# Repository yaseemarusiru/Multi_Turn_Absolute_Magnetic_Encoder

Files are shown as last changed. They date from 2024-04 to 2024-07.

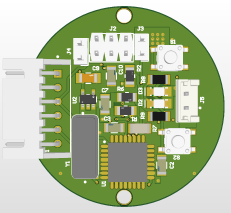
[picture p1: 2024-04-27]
PCB/Encoder PCB/Project Outputs for EDR/PCB_Photos/bottom.png

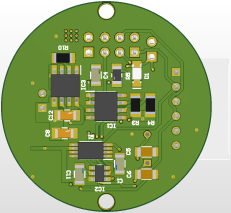
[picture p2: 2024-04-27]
PCB/Encoder PCB/Project Outputs for EDR/PCB_Photos/top.png

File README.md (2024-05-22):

# Multi_Turn_Absolute_Magnetic_Encoder
This repository contains all the documents of the project in which we made a multi turn absolute magnetic encoder.

Project team members :
  - <a href="https://github.com/YasodaLAE" target="_blank">Yasoda Lasiru</a>
  - Yaseema Rusiru (myself)
    




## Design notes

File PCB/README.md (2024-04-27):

This folder contains the design files of the PCB we designed using ALtium for this project.

There are 6 schematics in our project. 
  - Microcontroller.SchDoc
  - Voltage Regulator.SchDoc
  - Encode Schematic.SchDoc
  - Hall Effect IC.SchDoc
  - Battery Charger.SchDoc
  - Battery Protection.SchDoc

PCB file is renamed as PCB1.PcbDoc

You can check photos of the PCB in the Project Outputs for EDR folder.

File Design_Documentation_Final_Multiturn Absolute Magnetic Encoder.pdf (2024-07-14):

### Department of Electronic and Telecommunication Engineering University of Moratuwa

### Design Documentation

# Multi-turn Absolute Magnetic Encoder

Epa Y.L.A. | 210156U
Epa Y.R.A. | 210157A

This report is submitted as a partial fulfilment of module EN2160

June 2024

Design Documentation

## Contents

Comprehensive Design Details | 3
1 Introduction | 3
2 Electronics Documentation | 4
3 Enclosure Design | 24
4 Software Documentation | 45
Appendix | 50
A Daily Log | 50

# Comprehensive Design Details

## 1 Introduction

Encoders are devices that convert one form of information into another. They work by detecting the rotation or linear motion of a shaft or axle and converting it into a signal that can be interpreted by a control system. This signal can be used to monitor the position, speed, and direction of the shaft or axle, and to control its motion with high precision.

There are several types of encoders, including incremental encoders, absolute encoders, rotary encoders, and linear encoders.

Incremental encoders provide information about the motion of the shaft, including its direction and the distance it has moved, while absolute encoders provide the exact position of the shaft at any given time. Rotary encoders are used for rotary motion and can be either incremental or absolute, while linear encoders are used for linear motion.

Encoders have a wide range of applications in various industries including manufacturing, automation, aerospace, healthcare and entertainment. They are used in robotics, CNC machines, motors, tachometers, user interfaces and many other systems that require precise control and monitoring of motion and position. Encoders help improve the efficiency, accuracy and safety of machines and systems and they play a crucial role in enabling automation and advanced manufacturing technologies.

### 1.1 Types of Encoders

- Rotary Encoders

– Incremental Rotary Encoders: Measure the change in position from a reference point. They produce two square waves that help determine the direction and distance of rotation. These have a disc with alternating opaque and transparent sectors. As the disc rotates, an LED shines through the sectors, and a photo detector on the other side generates pulses. The number of pulses counted per unit time determines the speed, and the direction can be determined by the phase difference between two output signals.

– Absolute Rotary Encoders: Provides a unique code for each position. These can determine the exact position without requiring a reference point. Also, these have a disc with multiple tracks each with a unique pattern. Each track corresponds to a binary bit of the position code. The combination of all tracks gives a unique binary code for each position.

- Linear Encoders

– Incremental Linear Encoders: Similar to incremental rotary encoders but measures linear displacement. These encoders use a scale with equally spaced marks and a read head that moves along the scale. As the read head moves, it detects the marks and generates pulses.

– Absolute Linear Encoders: Provide an absolute position along a linear path. These encoders use a scale with a unique pattern along its length and a read head that reads the pattern. The pattern provides a unique position code.

- Optical Encoders: These use light (typically LEDs and photodetectors) to detect position changes. Commonly used in high-precision applications.
- Magnetic Encoders: Use magnetic fields to detect position changes. They are robust in harsh environments and less sensitive to dust and other contaminants.

From these types, we are designing a multi turn absolute magnetic encoder.

### 1.2 Uses of Encoders

Encoders are used in various fields for different applications. Below are some common ones.

- Industrial Automation

– Position and speed control in machinery.

– Feedback for robotic arms and CNC machines.

- Consumer Electronics

– Volume controls in audio equipment.

– User interface controls in various devices.

- Automotive Applications

– Steering angle sensors.

– Engine position sensors.

- Aerospace

– Position feedback in control systems.

– Monitoring the position of control surfaces.

- Medical Equipment

– Position sensing in imaging equipment.

– Feedback in robotic surgery tools.

This section includes a detailed description of the electronic components and circuitry of multi-turn absolute magnetic encoder.

## 2 Electronics Documentation

### 2.1 Components Selection

Our main components include selecting a hall effect sensor IC, a magnet for the placement on the shaft, a microcontroller and power management circuit components which includes a battery and power regulation and management ICs.

### 2.1.1 Sensing Circuit

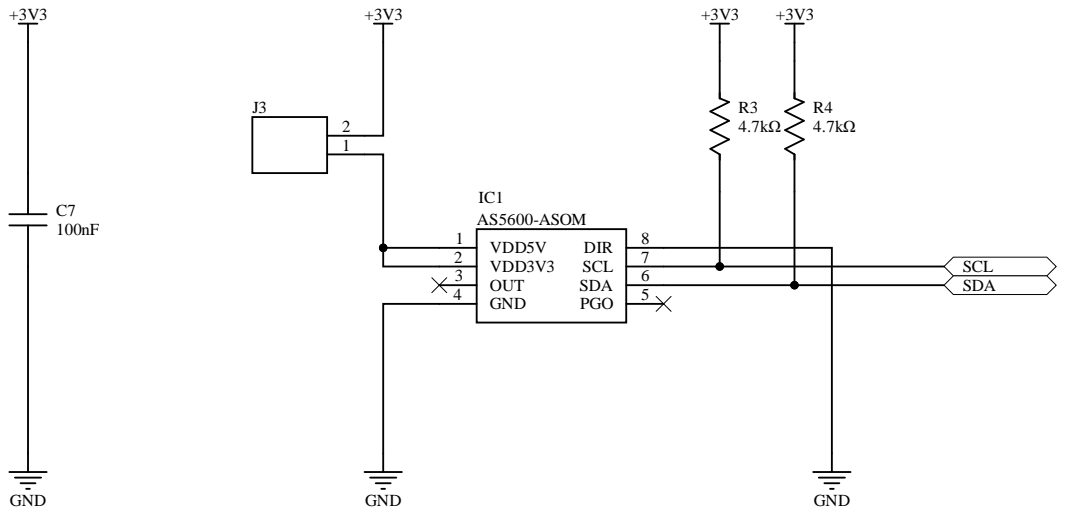
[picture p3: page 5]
Title; Size; Number; Revision; Date:; Sheet of; File:; F:\Altium Projects\..\Hall Effect IC.SchDoDc rawn By:; VDD5V 1 VDD3V3 2 OUT 3 GND 4; DIR; SCL; SDA; PGO; IC1 AS5600-ASOM; GND; SCL SDA; Yasoda Lasiru

Hall Effect IC

Through the sensing circuit, we detect the magnetic field change of a diametrically magnetized magnet using hall effect sensor IC which is placed on axis to the magnet. Important information such as the specifications of the magnet to select, according to the hall effect sensor IC, the air gap between the IC and the magnet etc. are presented below. They were obtained after a thorough analysis of the datasheet of the select hall effect sensor IC - AS5600 - which is manufactured by a leading company in the field -AMS OSRAM.

AS5600 hall effect sensor IC works in 3.3V. For that we have to connect VDD5V and VDD3V3 together and connect to 3.3V. A separate power isolation jumper J3 is used here so that we can disconnect the hall effect IC from the ATMega328p while we are programming the microcontroller. To pull up the I2C lines SCL and SDA, we have used R3 and R4 which are 4.7kΩ . This value is selected as per the datasheet of AS5600. Since we are reading the angle value through I2C we do not need to use OUT pin - which outputs the angle value in a PWM signal. PGO pin is used to enter the programming mode of the AS5600. Since we are using the default configurations, we won’t be needing that pin as well. The C7 100nF capcitor is use between the power lines according to the recommendation of the datasheet.

AS5600 Hall Effect Sensor

AS5600 is a Hall-effect based rotary magnetic position sensor. It uses planar sensors that convert the magnetic field component perpendicular to the surface of the chip into a voltage. The signals coming from the Hall sensors are first amplified and filtered before being converted by the analog-to-digital converter (ADC) inside the IC.

This sensor IC measures the absolute angle of a diametric magnetized on-axis magnet. The chip contains 4 hall effect sensors arranged in a circle. Together, they can detect changes in the direction of the magnetic field.

- Resolution of 12 bits
- temperature range of -40°C to 125°C
- supply voltage range -0.3V to 6.1V
- power continuous consumption of 50mW at 70°C
- Analog and PWM outputs
- PWM output frequency upto 920Hz
- I2C interfacing option
- programmable start and zero angle
- automatic entry into low power mode operation

There are various hall effect sensor ICs in the global market to choose from. Below are the criteria which led to the selection of the AS5600 magnetic hall effect sensor IC.

- Output Resolution: The AS5600 has a 12-bit digital to analog conversion (DAC) output resolution
- Maximum Angle Programmable: You can program the maximum angle from 18 to 360 degrees

- Selectable Output: The AS5600 provides an analog output ratiometric to VDD or PWM-encoded digital output
- Low-Power Consumption: The AS5600 has a smart low power mode feature to automatically reduce the power consumption
- Easy Setup: The AS5600 has automatic magnet detection
- Robust Environmental Tolerance: The AS5600 is qualified for a temperature range from -40°C to 125°C
- Magnet Airgap: The typical airgap is between 0.5 mm and 3 mm, and it depends on the selected magnet. A larger and stronger magnet allows a larger airgap

Magnet

According to the AS5600 data-sheet, the recommended specifications of the magnet are as follows.

- Diametrically magnetized: cylindrical
- Any one of diameter 6mm and thickness of 2.5mm, diameter 8mm and thickness of 3mm or diameter 8mm and thickness of 4mm
- magnetic input range should be between 30-90mT

We have selected a cylindrical neodymium magnet of diameter 6mm and thickness of 2.5mm.

### 2.2.1 Microcontroller Circuit

We have used a switch S1 to reset the microcontroller. It’s pulled up through R1 10kΩ resistor and connected to ground through C3 100nF capacitor.

Also, we have used another switch in the circuit, which is used to manually tare the turned angle, used for debugging purposes. Same as S1, it’s pulled up through R2 10kΩ and connected to ground through C4 100nF capacitor.

J2 is the programming port which is used to program the microcontroller. These SPI pins are also connected separately to the communication port, which is available to the user. Since we aim to minimize power consumption, we are using Y1 8MHz crystal oscillator as per the recommendation of the datasheet. This is connected to ground through two 22pF capacitors - which are also chosen according to the datsheet.

We have also used 100nF capacitors here to suppress high frequency noise and stabilize the voltage.

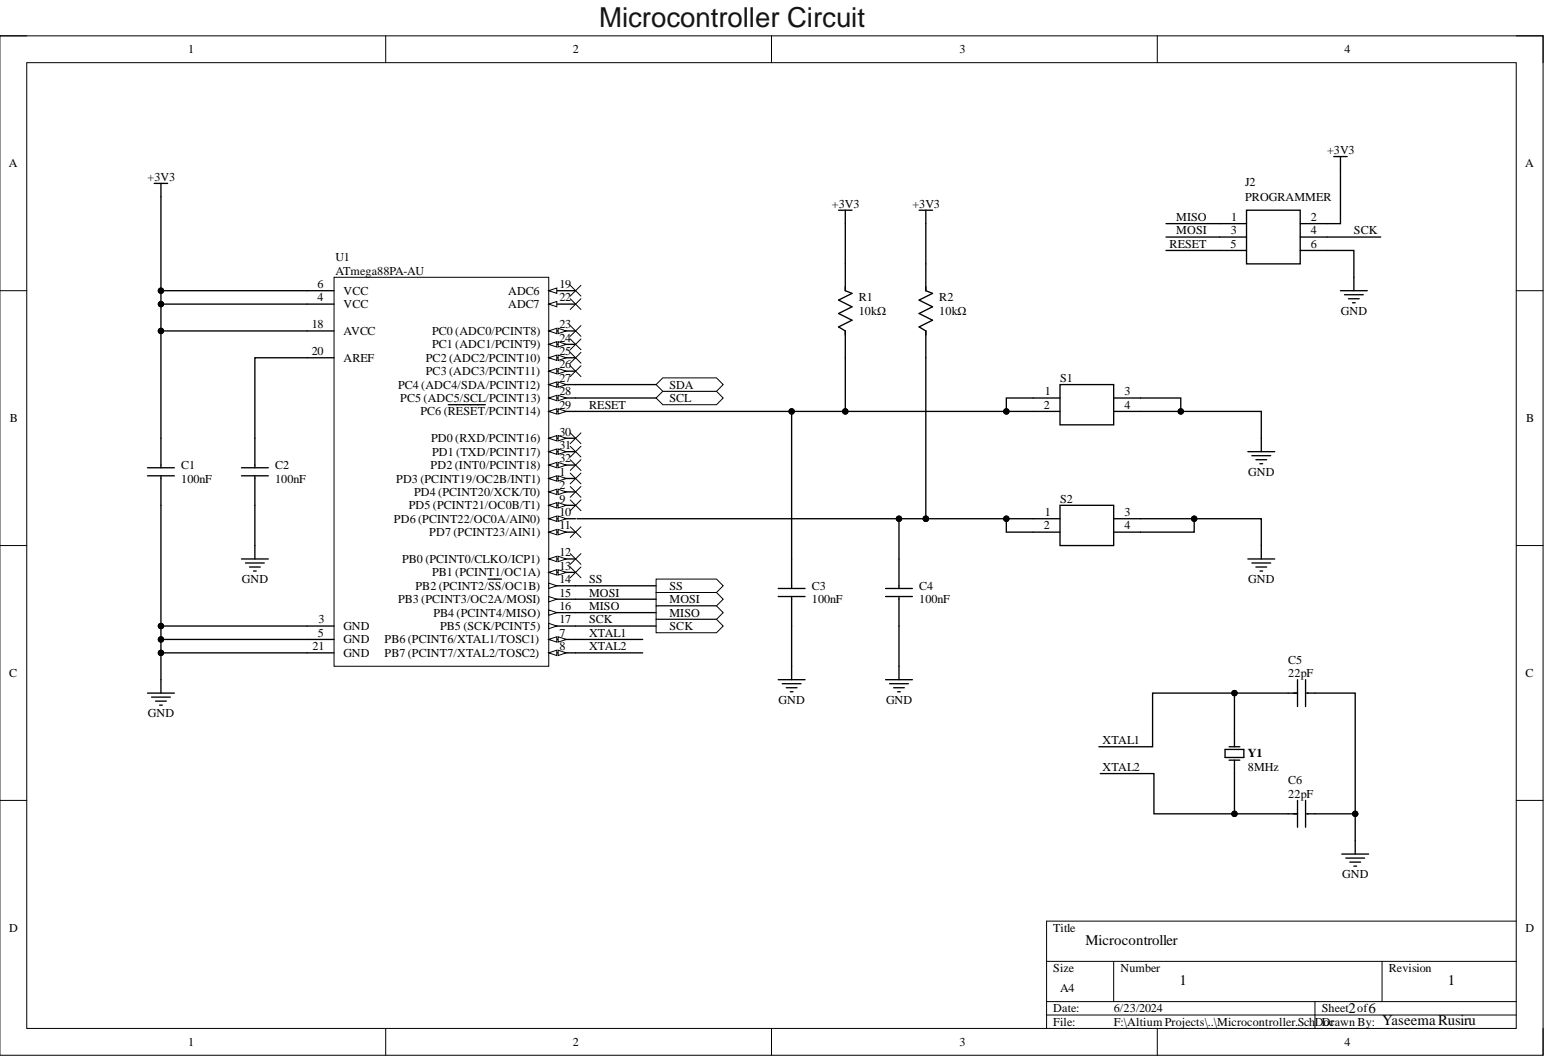
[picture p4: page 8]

ATMega328P-AU

We are using ATMega328P-AU as the micro-controller for our multi turn absolute magnetic encoder. It is a low power consuming microcontroller which can implement both SPI and I2C communication protocols at the same time, while saving power. It interfaces with the AS5600 sensor module to process position data and generate output signals. This includes the absolute angle and the algorithm to count the number of turns.

- 8 bit AVR RISC based
- 8KB flash memory 512B EEPROM and 1KB SRAM
- 10 bit ADC
- 8 bit timer/counter with prescalar and two PWM channels
- Internal calibrated oscillator

We have considered the following criteria when selecting thee microcontroller.

- CPU Architecture: The ATMega328P-AU is based on the AVR RISC architecture1. This architecture is known for its high performance and power efficiency
- Memory: The ATMega328P-AU has 32KB of in-system programmable flash memory, 1KB of EEPROM, and 2KB of internal SRAM. These are required for our application
- Operating Voltage: The ATMega328P-AU operates between 1.8-5.5V. We opted for 3.3V in order to run at a speed of 8MHz.
- Power Efficiency
- Seperate I2C and SPI bus availability to read AS5600 IC data while also giving the angle output to the user through SPI interface
- Availability

### 2.3.1 Power Management

As the main power supply for the hall effect sensor IC and the microcotroller, the user should input an external power source within the given voltage range (3.4V to 8V). Through this supply, the rechargeable battery charges, allowing the system to utilize its’ power even during power outages. For this we have implemented a separate charging circuit with over current and voltage protection.

Since we intend to use the microcontroller and the hall effect sensor IC with 3.3V supply, a voltage regulator is also to be used as part of the power management circuit. Moreover, we have utilized low power modes in both the microcontroller and the hall effect sensor IC in order to ensure that the power used is minimized. Furthermore this sub assembly consists of TP4056 and FS8205A ICs.

Voltage Regulator Circuit

J4 power isolation connector is used to isolate the microcontroller from the LDO while programming. So, we should power the microcontroller through the programming port while programming.

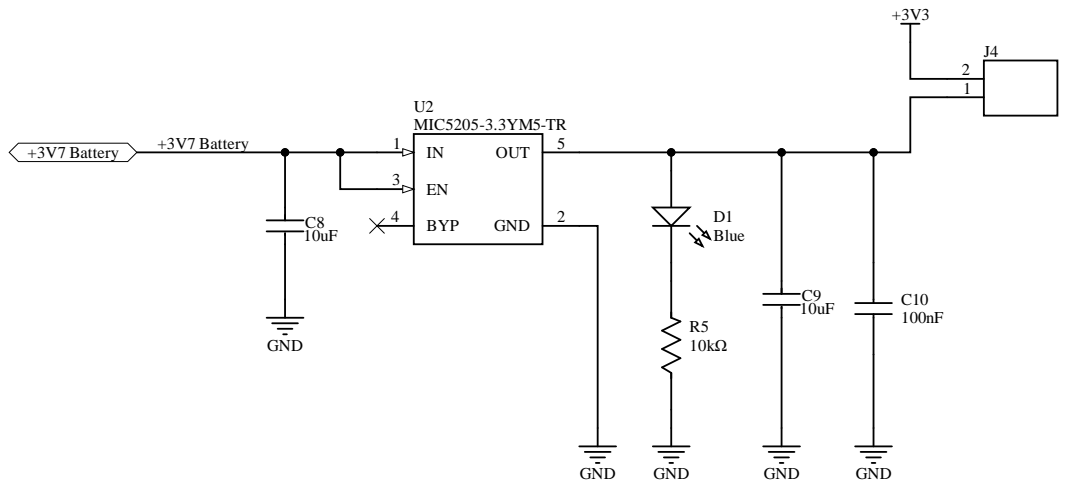
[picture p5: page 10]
Title; Size; Number; Revision; Date:; Sheet of; File:; F:\Altium Projects\..\Voltage Regulator.SchDDrawoc n By:; VoltageRegulator; BYP 4; OUT; GND; U2 MIC5205-3.3YM5-TR; +3V7 Battery +3V7 Battery; Blue; Yasoda Lasiru

We have used D1 blue diode to indicate whether power is available - specifically 3.3V which is available at the OUT pin. Here we have used 10kΩ resistor to minimize the current used by the diode. The datasheet of MIC5205-3.3YM5-TR LDO specifically mentions to use a capacitor value greater than 2.2 uF between ground and the OUT pin.

Since enable/shutdown is not required in our application, we have connected IN and EN pins (according to the datasheet).

Since noise is not a major concern BYP pin is not connected according to the datasheet. To handle the input voltage fluctuations, C8 10uF capacitor is used.

MIC5205-3.3YM5-TR Low-dropout Voltage Regulator

The MIC5205-3.3YM5-TR is a low-dropout (LDO) voltage regulator. It is designed to deliver a fixed output of 3.3V. This LDO regulator is commonly used in battery-powered devices due to its low quiescent current of 10nA and it provides good line and load regulation characteristics.

- Operating temperature range -40 - 125°C
- 150mA typical output current
- Output Voltage Accuracy: The MIC5205-3.3YM5-TR offers better than 1% initial accuracy
- Low Dropout Voltage: The MIC5205-3.3YM5-TR as a very low dropout voltage (typically 17 mV at light loads and 165 mV at 150 mA)12. This low dropout voltage allows the regulator to operate efficiently even when the input voltage is only slightly above the output voltag
- Temperature Coefficient: The MIC5205-3.3YM5-TR has a very low temperature coefficient
- Load and Line Regulation: The MIC5205-3.3YM5-TR provides extremely tight load and line regulation

Battery Charger Circuit

A high input in the CE pin will put the TP4056 in the normal operating mode. Hence, we have attached VCC to CE pin. The positive terminal of the battery should be connected to the BAT pin.

PROG pin is used to set the constant charge current and it can be used to monitor the charge current. This pin is grounded through a 2kΩ resistor. It sets the charging current which is 580mA according to the datasheet. BAT pin provides charge current to the battery and provides regulation voltage of 4.2V. When the voltage of the VIN pin drops to within 30mV of the BAT pin voltage, TP4056 enters low power sleep mode. This drops the BAT pin’s current to less than 2uA.

We can get an idea about the charging state of the battery through the intensity of the D2 and D3 LEDs.

Charge state | Orange LED | Green LED
charging | ON | OFF
Charge Termination | OFF | ON
Vin too low/ no battery | OFF | OFF

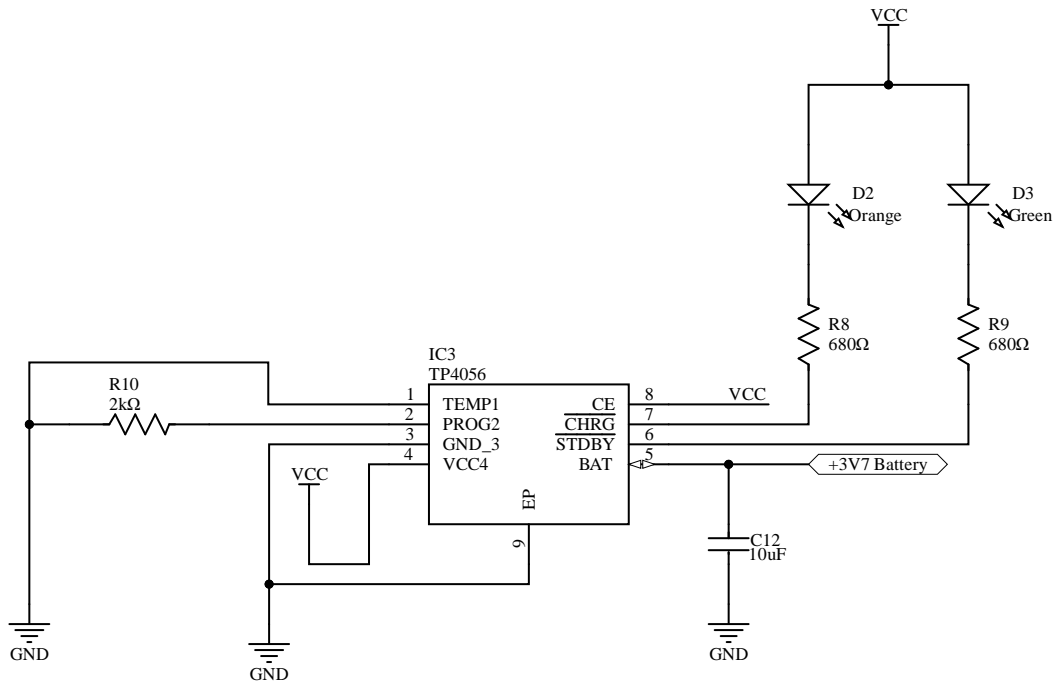
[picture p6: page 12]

TP4056 Constant Current Constant Voltage Linear Charger IC

The TP4056 is a standalone linear charger IC designed for single cell lithium-ion batteries. The charge current can be programmed externally with a single resistor. We have used 2kΩ for this. As per the datasheet, the charging current then becomes 580mA.

- Programmable charge current upto 1A
- Linear charger for single cell Lithiom Ion batteries
- Constant current
- Constant voltage
- Input supplt voltage -0.3V - 8V
- Maximum junction temperature 145
- Operating temperature range -40 - 85°C

Battery Protection Circuit

External battery can be connected to the circuit through J5. Positive and negative terminals of the battery are connected to VCC and GND pins through R6. C1 and R6 are selected according to the specifications given in the datasheet. R7 resistor value is also given in the datasheet. Since TD pin is used for testing purposes, it is not used. CS input pin is used for current sensing and detecting the charging.

Both S1 1 pin and S1 2 pin are the same. Both S2 1 pin and S2 2 pin are the same. G1 is the gate of one N channel MOSFET. G2 is the gate of the other N channel MOSFET. S1 1 is the source of the first MOSFET, S2 1 is the source of the second MOSFET. Hence these pins are grounded here. OD pin of DW01A-G is used to connect MOSFET gate for discharge control. OC pin is also connected to a MOSFET gate for charge control.

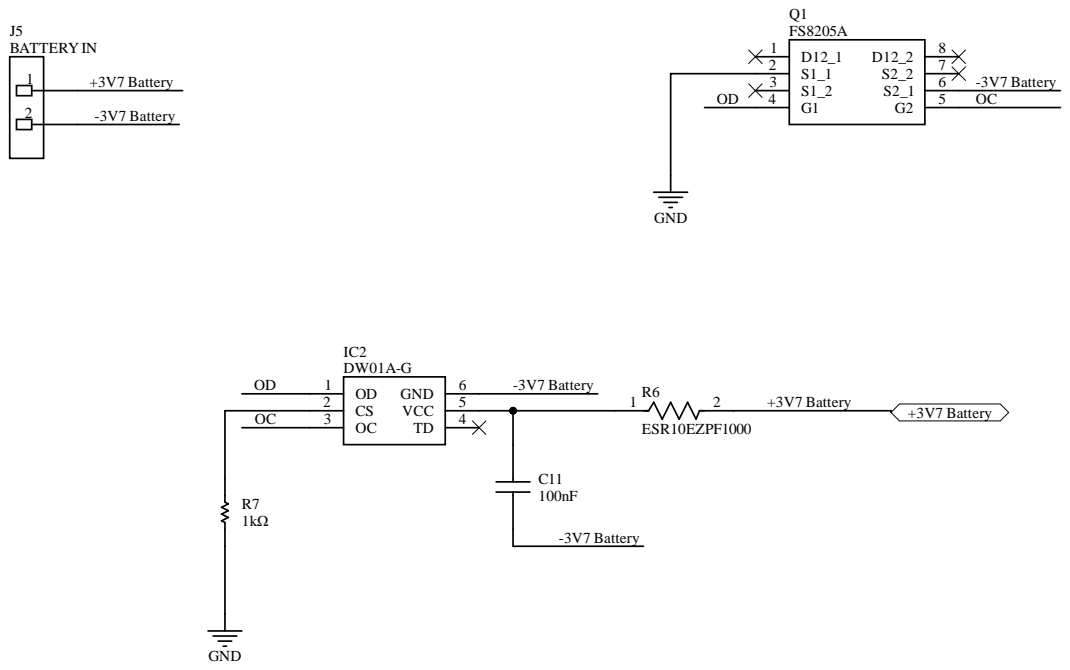
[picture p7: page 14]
Title; Size; Number; Revision; Date:; Sheet of; File:; F:\Altium Projects\..\Battery Protection.ScDhDrawoc n By:; J5 BATTERY IN; -3V7 Battery; GND; VCC; +3V7 Battery; Battery ProtectionCircuit; ESR10EZPF1000; YaseemaRusiru

FS8205A Dual N Channel Power MOSFET

This IC is used to ensure safe and efficient charging and discharging of the battery, preventing overcharging or excessive discharge which could damage the battery.

- Drain source voltage 20V
- Continuous drain current at 25°C - 6A
- Total power dissipation at 25°C - 1W
- Operating junction temperature range -55 to 150°C

DW01A-G Battery Protection IC

The DW01A-G is a one cell Lithium-ion/Polymer battery protection IC. It is designed to protect lithium-ion/polymer batteries from damage or degrading the lifetime due to overcharge, overdischarge, and/or overcurrent for one-cell lithium-ion/polymer battery powered systems. The DW01A-G ensures that the battery operates within its safe limits, thereby extending its lifespan and maintaining its performance

- Overcharge detection voltage 4.30±0.05V
- Overcharge release voltage 4.10±0.05V
- Overdischarge detection voltage 2.40±0.10V
- Overdischarge release voltage 3.00±0.10V
- Supply current at 3.9V VCC typical 3µA max 6µA

### 2.7 Functional Block Diagram

Figure 1: Functional Block Diagram of the Selected Design

### 2.8 System Overview

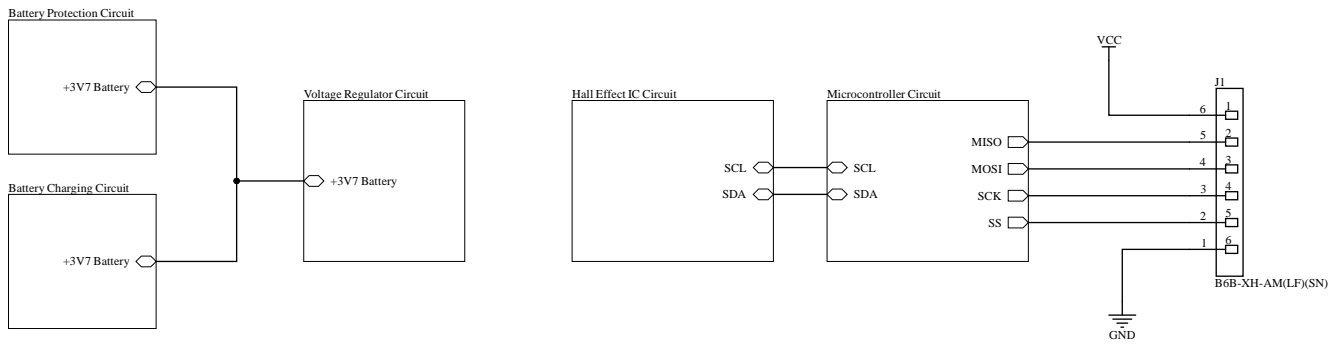
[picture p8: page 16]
Title; Size; Number; Revision; Date:; Sheet of; File:; F:\Altium Projects\..\Encode Schematic.SchDDrawocn By:; MOSI; MISO; SCK; SCL; SDA; Microcontroller Circuit; +3V7 Battery; GND; VCC; Encoder Circuit; YaseemaRusiru; PIJ101; PIJ102; PIJ103; PIJ104; PIJ105; PIJ106; COJ1

Battery Protection Circuit

Voltage Regulator Circuit

Hall Effect IC Circuit

Battery Charging Circuit

### 2.10 PCB Design

### 2.10.1 PCB Specifications

- Material: FR4
- Thickness: 1.6mm
- Copper Weight: 1 oz
- Radius : 18mm

2.10.2 2D Layout

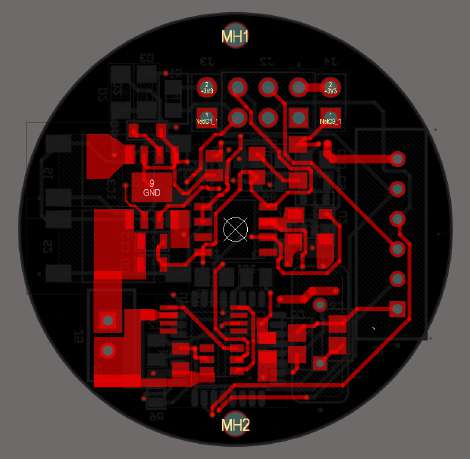
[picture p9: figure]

Figure 2: Top Layer

Figure 3: Bottom Layer

### 2.10.3 Before Soldering PCB

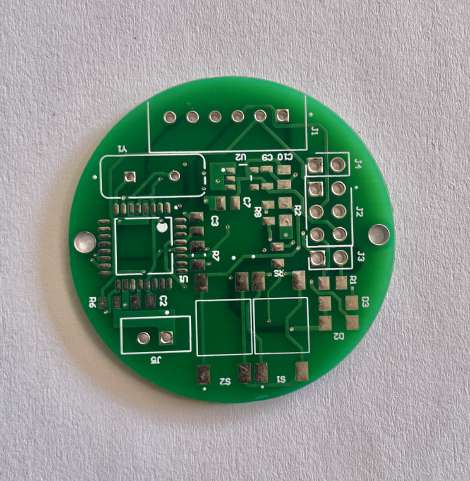
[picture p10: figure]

Figure 4: Bare PCB - Top

Figure 5: Bare PCB - Bottom

### 2.10.4 After Soldering PCB

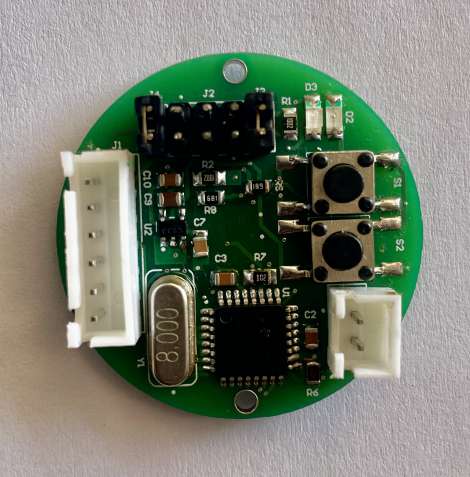
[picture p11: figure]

Figure 6: Soldered PCB

Figure 7: Soldered PCB

### 2.10.5 Photographs as evidence for the PCB testing

Here motor is controlled through raspberry pi and the encoder data is collected from the raspberry pi to be shown on the dashboard.

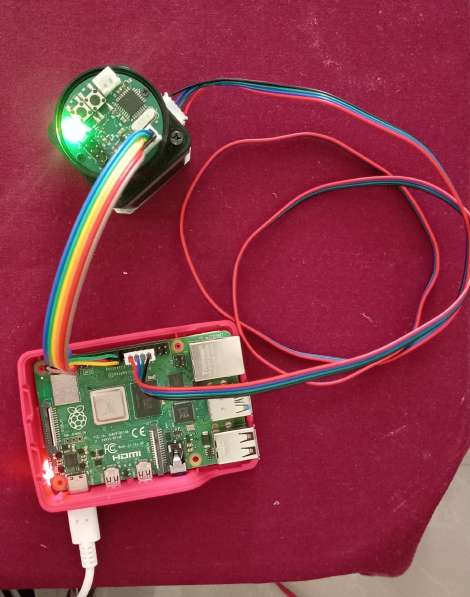
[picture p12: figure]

Figure 8: Testing

Figure 9: Testing

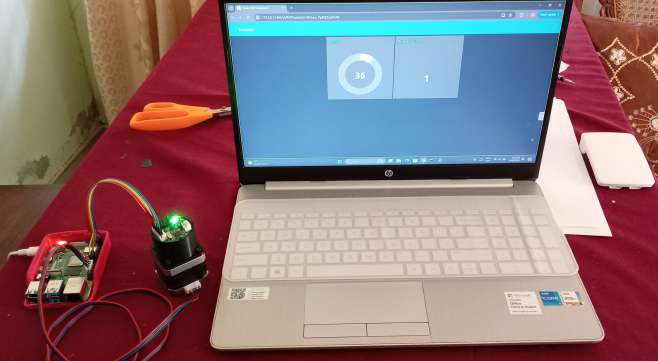
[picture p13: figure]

Figure 10: Testing

Figure 11: Testing

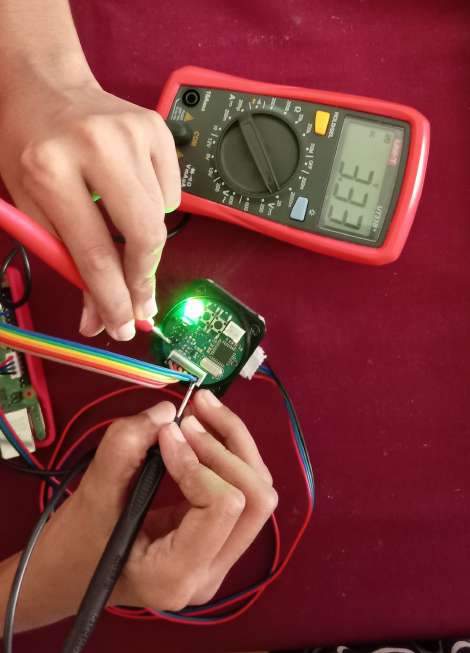
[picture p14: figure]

Figure 12: Testing

Figure 13: Testing

### 2.11 Bill of Materials

Designator | Description | Quantity
C1,C2,C3,C4,C7,C10,C11 | 16V 100nF X7R ±10% 0805 Multilayer Ce-ramic Capacitors MLCC - SMD/SMT ROHS | 7
C5,C6 | 16V 22pF ±5% 0805 Multilayer Ceramic Ca-pacitors MLCC - SMD/SMT ROHS | 2
C8,C9,C12 | 16V 10uF X7S ±10% 0805 Multilayer Ce-ramic Capacitors MLCC - SMD/SMT ROHS | 3
D1 | 25mA -30℃ +85℃ Positive post 460nm 469nm Blue 120° 80mW 1206 Light Emitting Diodes (LED) ROHS | 1
D2 | 25mA -30℃ +85℃ 601nm 603nm Positive post Orange 120° 55mW 1206 Light Emit-ting Diodes (LED) ROHS | 1
D3 | 25mA 516nm 525nm -30℃ +85℃ Positive post Emerald 120° 80mW 1206 Light Emit-ting Diodes (LED) ROHS | 1
IC1 | AS5600-ASOM | 1
IC2 | DW01A-G | 1
IC3 | TP4056 | 1
J1 | CONN HEADER VERT 6POS 2.5MM | 1
J2 | Push-Pull,P=2.5mm Wire To Board Connec-tor ROHS | 1
J3,J4,J5 | CONN HEADER VERT 6POS 2.5MM | 3
Q1 | FS8205A MOSFET(N CHANNEL) | 1
R1,R2,R5 | RES SMD 10K OHM 0.5% 1/8W 0805 | 3
R3,R4 | RES SMD 4.7K OHM 0.5% 1/8W 0805 | 2
R6 | RES SMD 100 OHM 0.5% 1/8W 0805 | 1
R7 | RES SMD 1K OHM 0.5% 1/8W 0805 | 1
R8,R9 | RES SMD 680 OHM 0.5% 1/5W 0805 | 1
R10 | RES SMD 2K OHM 0.5% 1/8W | 1
S1,S2 | 6mm 5mm Round Button 50mA Brick nog-ging 6mm SPST 12V SMD,6x6mm Tactile Switches ROHS | 2
U1 | 8-bit Microcontrollers -MCU AT-MEGA328PB 20MHZ IND TEMP | 1
U2 | IC REG LINEAR 3.3V 150MA SOT23-5 | 1
Y1 | Crystals 8MHz 20pF | 1

### 2.12 Design Specifications

The circuit operates at 3.3V. It can tolerate maximum 8V from the external source and this voltage also charges the battery. When the main power is not available, it switches the power source to battery. The MIC5205-3.3YM5-TR is a low-dropout (LDO) voltage regulator that outputs 3.3V. It requires an input voltage that’s at least 3.4V to account for the dropout voltage. Therefore, a 3.7V battery will be sufficient. Below are the required calculations when selecting it.

Battery Capacity: To calculate the minimum capacity of the battery, we need the total current consumption of the circuit.

Current consumption of main components:

- AS5600 Hall Effect Sensor: 1.5mA (typical)
- ATMEL ATMega328P-AU: 3mA (maximum)
- MIC5205-3.3YM5-TR: negligible
- TP4056: negligible
- FS8205A: negligible
- DW01A-G: negligible

Total current consumption = 1.5mA + 3mA = 4.5mA

If the device need to operate for 24 hours without external power(battery life), it would need a battery with a capacity of at least 4.5mA x 24 hours = 96mAh. The battery can be connected by the user, so the required capacity can be decided as per the following table.

Duration time (approximate) | Battery Capacity
24 hours | 96mAh
7 days | 672mAh
1 month | 2880mAh

The TP4056 charger IC decides the time taken for the battery to fully charge, by the external resistor connected to it. As per the datasheet of TP4056 charger IC we have used 2kΩ for that. So the charging current is documented as 580mA. As per the battery used by the user, the charging time varies. If the user takes 1800mAh 3.7V battery it will take 1800/580 = 3 hours approximately to fully charge the battery.

## 3 Enclosure Design

### 3.1 SolidWorks Design

Model Tree - Part 1

25

Model Tree - Part 2

26

Enclosure Base

27

Enclosure Base

28

Base Part Mold Design

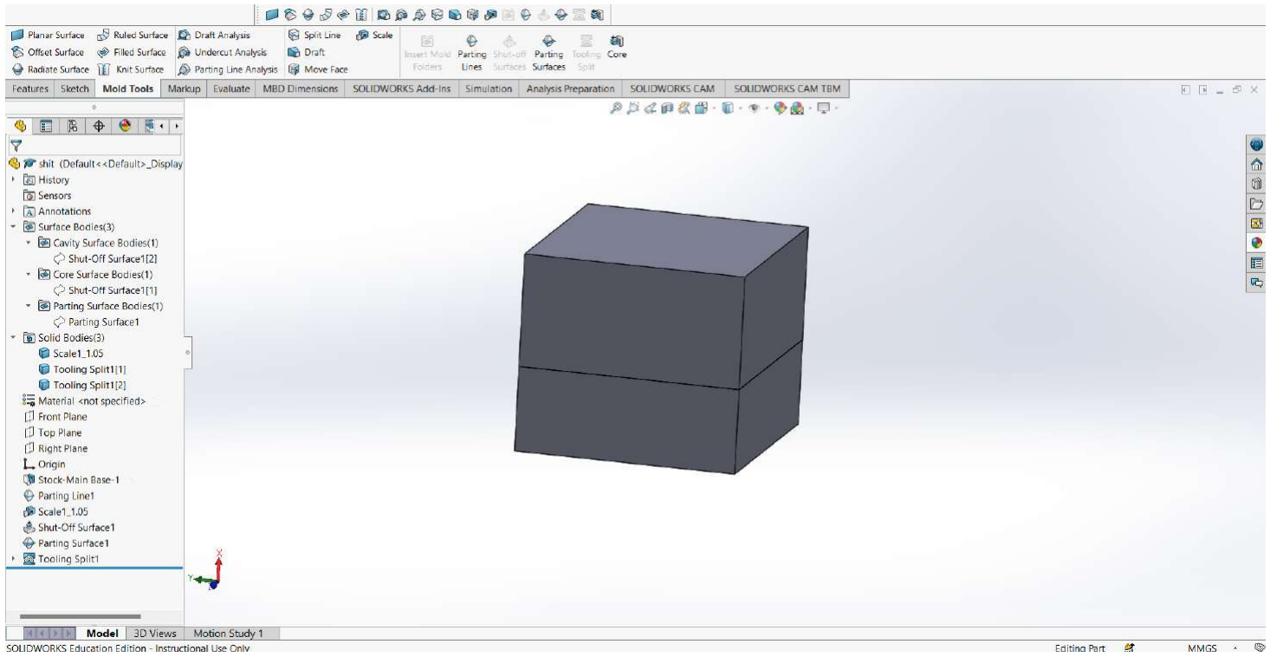
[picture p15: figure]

29

Base Part Mold Design

30

Enclosure Lid

32

Lid Part Mold Design

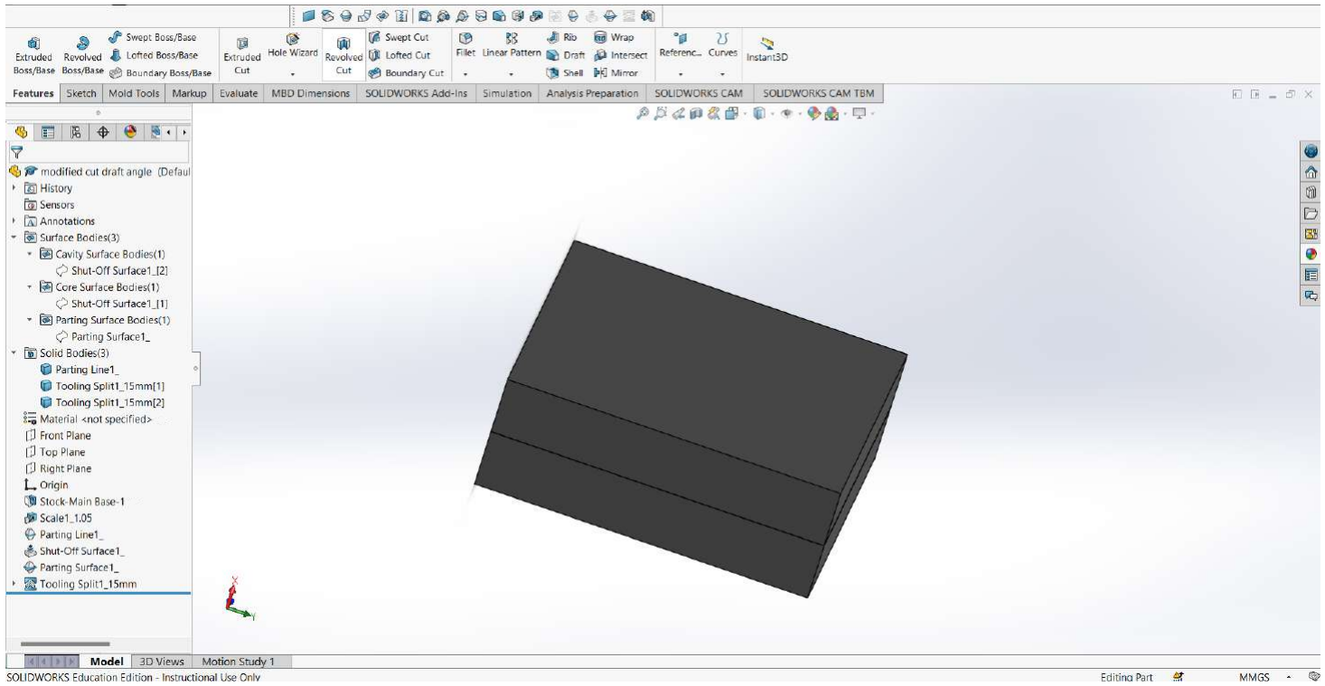
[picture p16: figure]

33

Lid Part Mold Design

34

Assembly : Exploded View

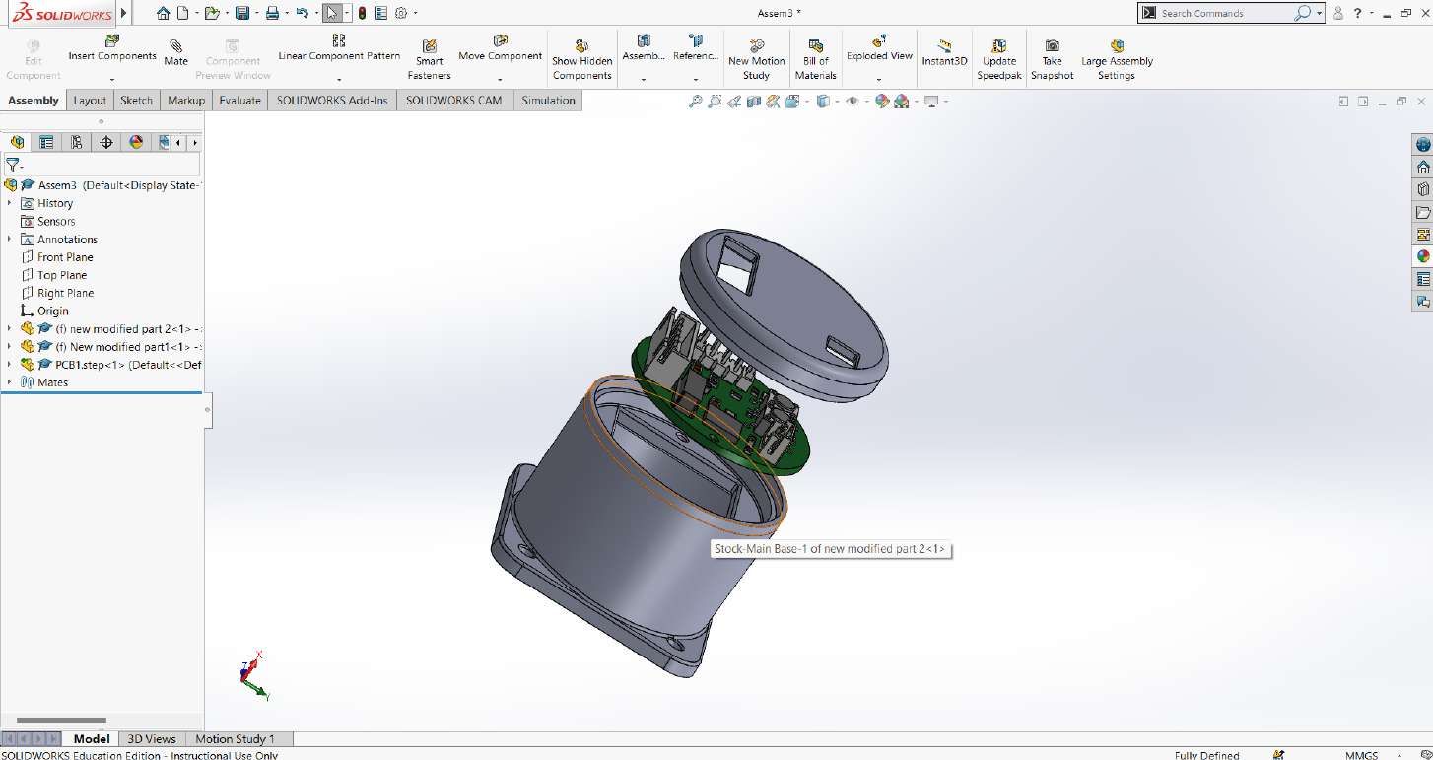
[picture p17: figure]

36

Assembly

37

Assembly and Design Drawings

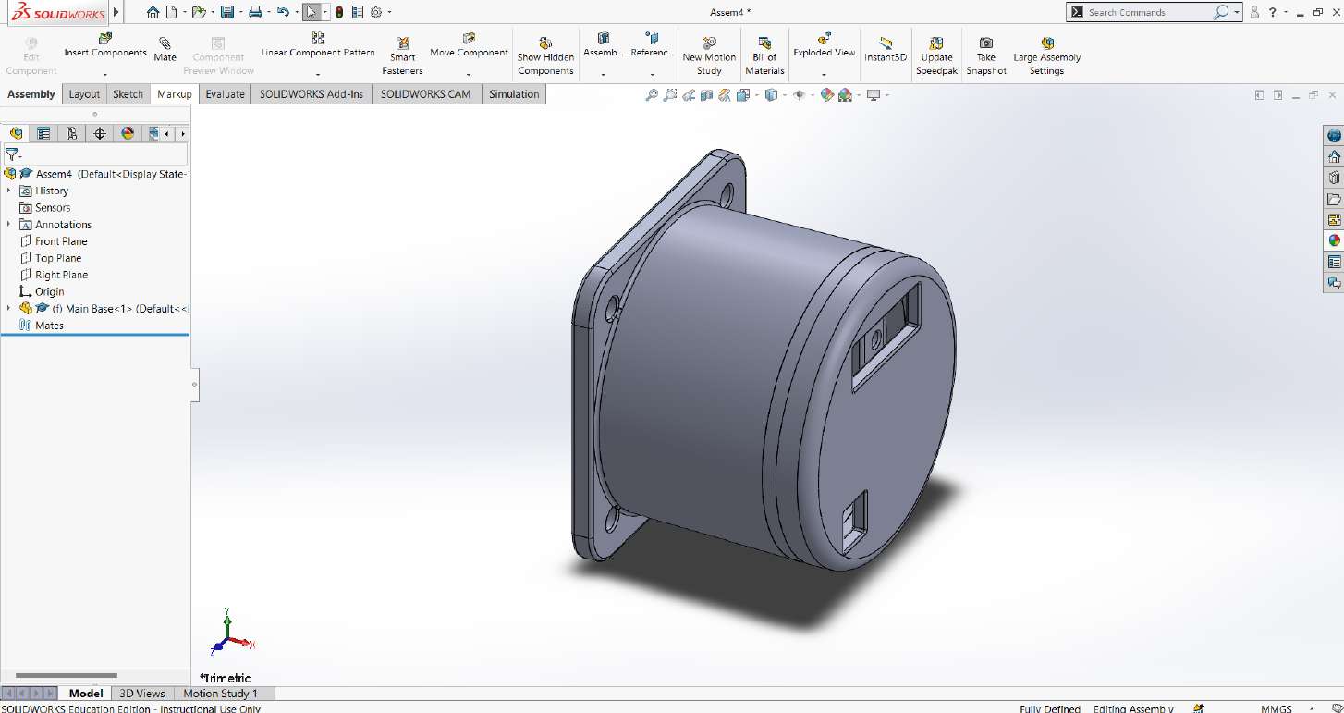
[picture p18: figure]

38

2

3

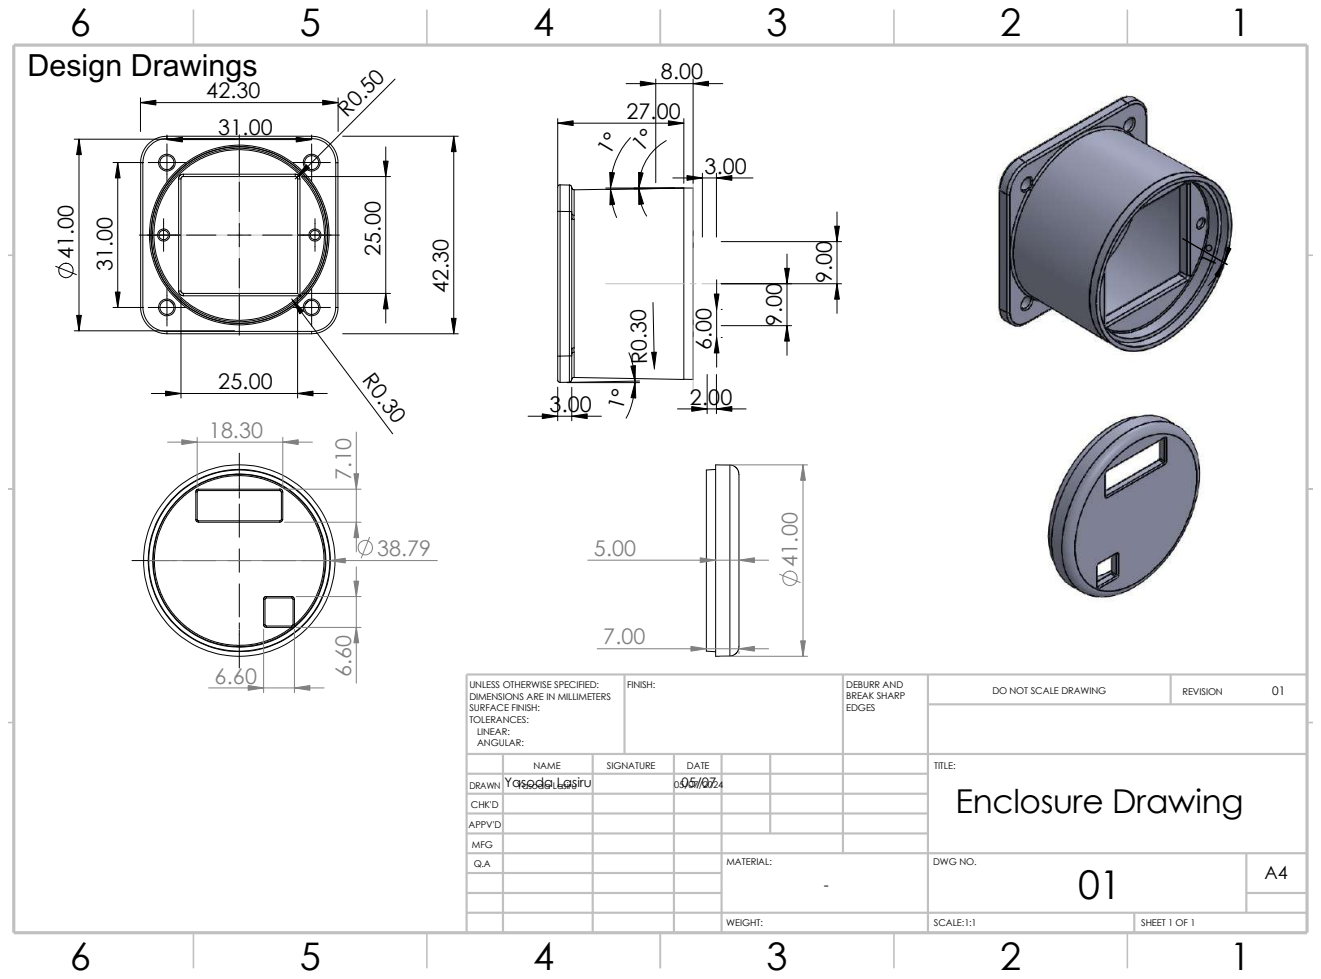
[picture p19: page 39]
FINISH:; EDGES; DO NOT SCALE DRAWING; REVISION; SCALE:1:1; SHEET 1 OF 1; WEIGHT:; DEBURR AND BREAK SHARP

UNLESS OTHERWISE SPECIFIED:
DIMENSIONS ARE IN MILLIMETERS
SURFACE FINISH:
TOLERANCES:
LINEAR:
ANGULAR:

NAME | SIGNATURE | DATE | | | | TITLE: Enclosure Drawing
Yasoda Lasiru | | 05/07 05/07/2024

MFG | | | | | | | 1 DRAWN
CHK'D
APPV'D

Q.A | | | | MATERIAL: - | DWG NO. 01 | A4

### 3.2 Photographs of Physically Built Enclosure

Figure 14: Enclosure

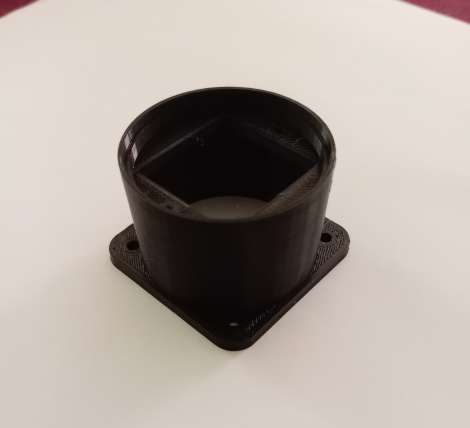
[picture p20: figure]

Figure 15: Enclosure

Figure 16: Enclosure

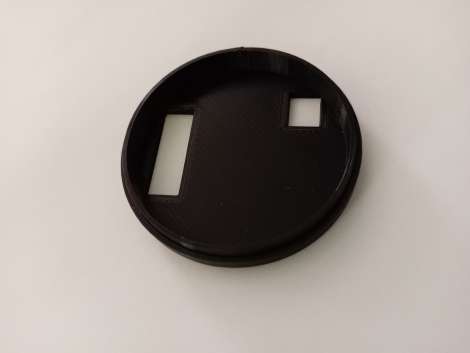
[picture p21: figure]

Figure 17: Enclosure

Figure 18: Enclosure

### 3.3 Photographs of System Integration

Below are steps to fix the encoder to the motor.

Figure 19: Fix coupler with magnet to the shaft

Figure 20: Fix the PCB to the main enclosure part

Figure 21: Now we have to fix this to the motor

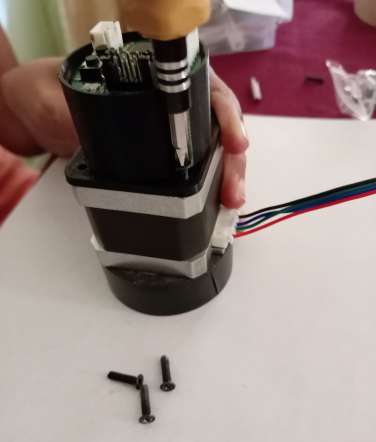
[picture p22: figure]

Figure 22: Fixing the screws

Figure 23: Fixing the screws

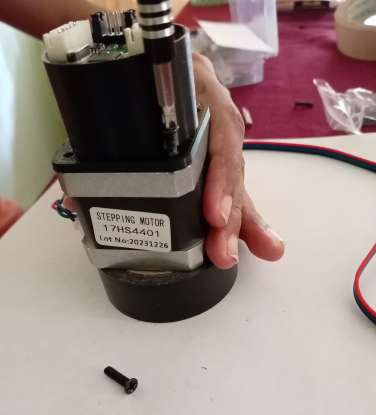
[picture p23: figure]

Figure 24: Fixing the screws

Figure 25: Fixing the screws

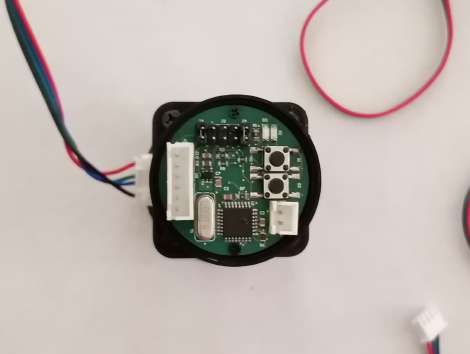
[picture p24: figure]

Figure 26: After fixing all the screws

Figure 27: Fix the lid

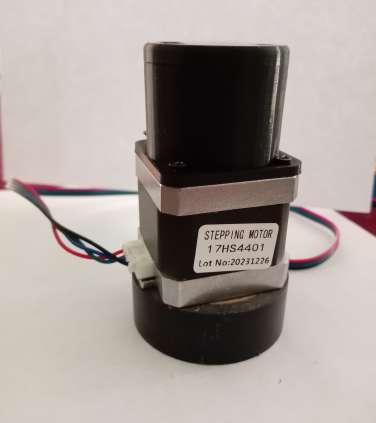
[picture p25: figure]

Figure 28: Side view after fixing

Figure 29: Now we can fix the communication port and battery input like this

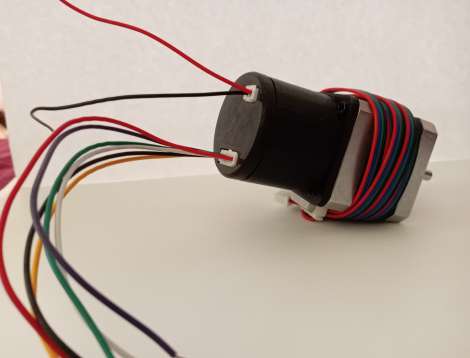
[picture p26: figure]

Figure 30: Side view

## 4 Software Documentation

Our encoder software should be accessible to the user outside reading the rotated angle. The main outputs should be the turned angle and the turns count. These values are output through the SPI protocol.

We have selected this protocol because of its’ fast response time, ability to be implemented in the ATMega microcontroller and the ease of implementation. Since we are communicating with the hall effect IC through I2C interface, SPI is the best option to avoid any potential conflicts. This has been implemented using C in Microchip Studio. The microcontroller reads the raw angle from the hall effect sensor IC and calculate the turns count, finally it outputs the angle and the turns count with three bytes, first two bytes dedicated for the angle.

Users can access these bytes via the SPI ports in the encoder and request bytes by the index. The pin mapping to access the SPI is as below.

- User MISO → MISO
- User MOSI → MOSI
- User CS → CS
- User CLK → CLK

The following code has been used inside the ATMega328p microcontroller to facilitate the communication between the user and the encoder. Interrupts have been used to provide the output the user whenever it is requested. Here the ATMega328p acts as the SPI slave. Readings from hall effect IC is taken in the loop function. For that, the ATMega328p is acting as the I2C master, since it is recommended to read through I2C protocol from the AS5600 hall effect sensor IC.

The angle value is a 16 bit value and can be accessed by sending 0x01 and 0x02 to the encoder. 0x01 will give the high 8 bits and 0x02 will give the low 8 bits. 0x03 returns the turns count which is also a 8 bit value.

#define F_CPU 8000000UL

#include <avr/io.h> | //Include AVR io

#include <avr/interrupt.h> //Include std interrupt

#define I2C_FREQ 100000L

#define AS5600_ADDRESS 0x36 // Default device I2C address

#define SS | PINB2 | //Define SPI pins

#define MOSI | PINB3

#define MISO | PINB4

#define SCK | PINB5

#define SCL | PINC5 | //Define I2C pins

#define SDA | PINC4

/* byte 1 : angle[15:8]
byte 2 : angle[7:0]
byte 3: turns[7:0] */

uint8_t byte1 = 0;
uint8_t byte2 = 0;
uint8_t byte3 = 0;

uint8_t q=0;
uint8_t preQ = 0;

uint16_t int1;
uint16_t int2;
uint16_t angle;

void delay_func(uint8_t count) { //delay function volatile uint8_t delay = 0;

while (delay < count) {
delay++;
}
}

void startI2C(uint32_t address) { //start I2C
TWCR = (1<<TWSTA)|(1<<TWEN)|(1<<TWINT); //Enable I2C and generate START condition
while(!(TWCR&(1<<TWINT))); //Wait until I2C finish its current work TWDR = address; //Write SLA+W in I2C data register
TWCR = (1<<TWEN)|(1<<TWINT); // Enable I2C and clear interrupt flag while (!(TWCR&(1<<TWINT))); // Wait until I2C finish its current work }

uint8_t getAngle(uint8_t reg){
uint8_t byte;

// Start I2C transmission to write the register address
startI2C((AS5600_ADDRESS << 1) | 0); // AS5600 address with write bit

TWDR = reg; //write register address to TWDR register
TWCR = (1<<TWEN)|(1<<TWINT); //clear interrupt flag
while (!(TWCR&(1<<TWINT))); //wait until interrupt flag is cleared

// Start I2C transmission to read the data
startI2C((AS5600_ADDRESS << 1) | 1); // Address with read bit

// Read byte
TWCR = (1<<TWEN)|(1<<TWINT); //clear interrupt flag again to start reading while (!(TWCR&(1<<TWINT))); //wait until read operation is complete
byte = TWDR; //read the received byte in TWDR register

// Stop I2C transmission
TWCR = (1<<TWSTO)|(1<<TWINT)|(1<<TWEN); //generate stop condition while (TWCR&(1<<TWSTO)); //wait until stop condition is executed

return byte;
}

int main(void){
DDRB &= ~((1<<MOSI)|(1<<SCK)|(1<<SS)); // Make MOSI, SCK, SS as input
DDRB |= (1<<MISO); | // Make MISO pin as output
SPCR |= (1<<SPE) ; | // Enable SPI in slave mode
SPCR |= (1<<SPIE); | // Enable SPI interrupts
SPDR = 0; | //clear SPI data first

sei(); //global interrupt enable

DDRC |= (1<<SDA)|(1<<SCL); //set SCL and SDA as output PORTC |= (1<<SDA)|(1<<SCL); //set SCL and SDA high

TWSR = 0x00; // Set pre scaler to 1
TWBR = ((F_CPU / I2C_FREQ) - 16) / 2; //initialize i2c frequency
ADCSRA = 0; | //disable ADC
PRR = (1<<PRTIM1)|(1<<PRTIM0)|(1<<PRTIM2); | //disable timers

while (1) {
byte1 = getAngle(0x0D); //get high byte
byte2 = getAngle(0x0C); //get low byte

int1 = (int) byte1;
int2 = (int) byte2;

uint16_t raw_angle = (int1<<8)|int2; //raw angle calculation - between 0 - 4096 (12 bit value)
angle = raw_angle*360/4096; //to get angle in 0-360 range

//update byte3
if (0<=angle && angle<=90) q = 1;
else if (90<angle && angle<=180) q = 2; else if (180<angle && angle<=270) q = 3;
else if (270<angle && angle<360) q = 4;
if (q!=preQ) {
if (q==1 && preQ==4) byte3++; //increase turns count if (q==4 && preQ==1) byte3--; //decrease turns count preQ = q;
}

delay_func(100);
}
return 0;
}

ISR (SPI_STC_vect){
uint8_t c = SPDR; //get the requested register name switch (c) {
case 0x01: //asking for byte1 (high byte)
SPDR = byte1;
break;

case 0x02: //asking for byte2 (low byte) SPDR = byte2;
break;

case 0x03: //asking for byte3 (turns count) SPDR = byte3;
break;
}
}

## References

[1] AMS AS5600 position sensor position sensors Datasheet - AMS-Osram ams. Available at: https://ams-osram.com/products/sensors/position-sensors/ams-as5600-position-sensor (https://ams-osram.com/products/sensors/position-sensors/ams-as5600-position-sensor) (Accessed: 15 May 2024).
[2] ATMEGA328P Datasheet. Available at: https://www.microchip.com/en-us/product/atmega328p (https://www.microchip.com/en-us/product/atmega328p)
[3] DW01A Datasheet. Available at: https://cxem.net/master/files/97 DW01A-DS-11 EN.pdf (https://cxem.net/master/files/97_DW01A-DS-11_EN.pdf)
[4] FS8205A Datasheet. Available at: https://www.ic-fortune.com/upload/Download/FS8205A-DS-12 EN.pdf (https://www.ic-fortune.com/upload/Download/FS8205A-DS-12_EN.pdf)
[5] TP4056 Datasheet. Available at: https://dlnmh9ip6v2uc.cloudfront.net/datasheets/Prototyping/TP4056.pdf (https://dlnmh9ip6v2uc.cloudfront.net/datasheets/Prototyping/TP4056.pdf)
[6] MIC5205 Datasheet. Available at: https://ww1.microchip.com/downloads/en/DeviceDoc/20005785A.pdf (https://ww1.microchip.com/downloads/en/DeviceDoc/20005785A.pdf)

# Appendix

## A Daily Log

- 28 Feb 2024

Final Project Proposal submitted

- 23 Feb - 26 Mar 2024

Review progress
A comprehensive study was conducted on the existing work in the industry regarding multi-turn absolute magnetic encoders. The study revealed that there are primarily two types of encoders available in the market: optical and magnetic encoders. Among these, magnetic encoders were found to be more prevalent due to their robustness, durability, and immunity to external factors such as dust and moisture.

Furthurmore, multi-turn magnetic encoders come in various configurations, including different resolutions, shaft sizes, and enclosure types. Some encoders only consisted of a PCB, requiring a specific mechanism to attach them to the motor. On the other hand, most encoders had enclosures that included a user interface (UI) to display additional information such as position, speed, and direction.

The study also highlighted the importance of enclosure design in ensuring the reliability and durability of the encoder. Some enclosures were designed to provide IP67 or IP68 protection against dust and water ingress, while others were designed to withstand harsh operating conditions such as high temperatures, vibrations and shocks.

Based on the findings , a detailed analysis was performed to identify the key design considerations for our multi-turn absolute magnetic encoder. The analysis included a comparison of different enclosure designs, shaft sizes, and UI options as well as an evaluation of their impact on the overall performance and reliability of the encoder. The results of this analysis will be presented in the design documentation.

- 27 Feb - 2 Mar 2024

Studied about how the EDR project can be extended for the development of the Sri Lankan Industry
It was observed that solid theoretical foundation is essential before attempting any project and working according to scientific principles is crucial for project success. Also, selecting suitable projects that align with the capabilities and resources of the Sri Lankan industry is vital for contributing to its development. To prevent future mistakes, we should focus more on understanding market and industry needs, as well as the unique challenges of the Sri Lankan industry.
- 4 Mar - 10 Mar 2024

Planned the Next Steps

Explored various circuits and methodologies to be used for our own design. These included three main types.

– Using a gearbox

There are several encoders in the market using gearboxes. The advantages of using a gearbox is that it doesn’t need a separate power source to function. The disadvantage is bulkiness it has and the complexness associated with making the gears. Apart from that it’s a good option.

Figure 31: Gear Box in an Encoder

– Using wiegand sensor This sensor is not currently available to purchase.

Figure 32: Wiegand Sensor in an Encoder

– Using battery backup

This seems to be the most practical option. But, this approach needs to minimize the power consumption a lot to have a significant efficiency compared to others.

- 10 Mar - 22 Mar 2024

Create Stakeholder Map and Observe Users

Identified the potential stakeholders related to our project. Studied about the various situations where multi turn absolute magnetic encoders are currently used. These include robotic arms, rotating shaft of motors etc.

- 23 Mar - 28 Mar 2024

Figure 33: Battery Backup Encoder

Enclosure Design Discussion
It was decided to have three main parts in our enclosure. They are separately, base part to fix to the motor, holder part for the PCB and battery and main housing part. These parts were discussed with details and rough designs were made.
- 29 Mar 2024

Battery Selection
Decided the battery specifications and calculations associated with it, to run the device for a longer time. Calculations are included in documentation.
- 23 Mar - 1 Apr 2024

Designing the circuit
After careful consideration, it was decided to implement a battery backup circuit for our multi-turn absolute magnetic encoder. The design criteria for the circuit were established and documented, taking into account the specific requirements of the AS5600 hall effect sensor IC, ATMEGA328p-AU micro controller and other main power consuming components.

To ensure accurate and reliable data transmission, it was decided to use the I2C protocol to read data from the AS5600 hall effect sensor IC and output it to the user through SPI protocol. This decision was based on the high precision and accuracy of the I2C protocol, as well as the analog output of the AS5600. By reading the SPDR data register using I2C, we can obtain the exact angle turned with 12-bit precision, making it a more convenient and reliable solution.

In addition to finalizing the circuit design, we also discussed the importance of conducting a power consumption test to verify that our design meets the low power consumption requirements. This test will involve measuring the power consumption of the circuit in various operating modes and comparing it to the design specifications. Based on the results of this test, we may need to make further optimizations to reduce power consumption and extend battery life.

- 1 Apr - 8 Apr 2024

Designed the schematics and finalized the PCB.

- 13 Apr 2024

Sent the PCB design files to manufacture

- 22 Apr 2024

Enclosure Design Discussion
Initially it was decided to go with three parts for the enclosure. It was decided to make a few changes to that and combine two of those for the ease of assembly and manufacturing. Now base part and PCB holding part will be combined to a single one and separate part will be designed as the lid.
- 22 Apr - 29 Apr 2024

Designed the enclosure with new changes.

- 30 Apr - 3 May 2024

Soldered the PCB

- 18 Mar - 4 May 2024

Coding

It was experimented with several algorithms to implement the communication between the user, ATMega IC and the hall effect sensor IC. First it was tried implementing the protocols without using interrupts, but with furthure experiment, interrupts turned out to be the appealing solution to manage both the protocols at once.

Here it was made Raspberry pi as the SPI master and ATMEGA328p-AU as the SPI slave. Also, ATMEGA328p would act as the I2C master for AS5600 hall effect sensor IC. It would read data from AS5600 through I2C and count the turns and then send the turned angle along with the number of turns to the raspberry pi through SPI. Raspberry pi was solely used for the purpose of interfacing and testing of our multi turn absolute magnetic encoder.

It was managed to successfully read the data through user interface even though initially we faced some difficulties in reading them. The SPI protocol seemed to not work properly when both the I2C and SPI protocols were being used inside the ATMEGA328p. With SPI running using vector interrupts, we were able to get both of the protocols running on the micro controller at the same time.

A sample code to test the encoder is been given below. This has been tested in a Raspberry Pi Model 4B.

test.c

#include <stdio.h>

#include <stdint.h>

#include <fcntl.h>

#include <sys/ioctl.h>

#include <linux/spi/spidev.h> #include <unistd.h>

#include <sys/mman.h>

#define SPI_DEVICE "/dev/spidev0.0" // Define SPI device path

#define GPIO_BASE 0x20200000 | // Define base address for GPIO pins

#define GPIO_LEN 0x1000 | // Define length of GPIO memory

volatile uint32_t *gpio; // Declare a pointer to a volatile uint32_t for GPIO access

void delay_func(uint32_t count)
{
volatile uint32_t numDelay = 0; while (numDelay < count)
{
numDelay++;
}
}
void setup_gpio() { | //setup gpio
int fd = open("/dev/mem", O_RDWR|O_SYNC); | //open mem location for
read write
if (fd<0) {
perror("Failed to open /dev/mem");
return;
}
gpio = (volatile uint32_t *)mmap(NULL, GPIO_LEN, PROT_READ|PROT_WRITE, MAP_SHARED, fd, GPIO_BASE); if (gpio == MAP_FAILED) {
printf("Failed to map GPIO memory");
close(fd);
return;
}
close(fd);
}

void gpio_set_output(int pin) {
volatile uint32_t *reg = &gpio[pin/10]; int shift = (pin%10)*3;
*reg = (*reg & ~(7<<shift))|(1<<shift); }

void gpio_write(int pin, int value) {
if (value)
gpio[7] = 1<<pin;// address of the GPIO register for the given pin
// shift value
else | //write to gpio
gpio[10] = 1<<pin;
}

unsigned char spi_transfer(int fd, unsigned char tx) { unsigned char rx;
struct spi_ioc_transfer tr = {
.tx_buf = (unsigned long)&tx, //set transmit and receive buffers .rx_buf = (unsigned long)&tx,
.len = 1,
};

ioctl(fd, SPI_IOC_MESSAGE(1), &tr); //SPI transfer
return tx; | //return returned value
}

int main() {
setup_gpio(); | //set up
gpio_set_output(0);
int fd = open(SPI_DEVICE, O_RDWR); //open for read write if (fd < 0) {
printf("Failed! No SPI device.");
return 1;
}
uint8_t mode = SPI_MODE_0; | //SPI mode
uint8_t bits = 8; | //num bits
uint32_t speed = 2000000; | //2MHz speed
if(ioctl(fd, SPI_IOC_WR_MODE, &mode)<0||ioctl(fd, SPI_IOC_WR_BITS_PER_WORD, &bits)<0||ioctl(fd, SPI_IOC_WR_MAX_SPEED_HZ, &speed)<0){ // Write the SPI speed printf("Failed!");
close(fd);
return 1;
}
while (1) {
gpio_write(0, 0); | // enable Slave Select
unsigned char a = spi_transfer(fd, 0x01); | //read first byte from
reguster
unsigned char b = spi_transfer(fd, 0x02); //read second byte from reguster
unsigned char c = spi_transfer(fd, 0x03); //read third byte from reguster

gpio_write(0, 1); // disable Slave Select delay_func(1000); // delay
gpio_write(0, 0); | // enable Slave Select
int numberOfTurns = (int) c; | // convert to integer
int finAngle = ((int)a<<8)|(int) b; | // construct the 2 byte
integer

gpio_write(0, 1); // disable Slave Select

printf("Number of Turns: %d\n", numberOfTurns); //print found values
printf("Angle from 0 to 360: %d\n", finAngle); delay_func(1000); // delay
}
close(fd);
return 0;
}

- 20 May - 24 May 2024

Made a dashboard
Made a dashboard to display the readings from the encoder (turned angle and the number of turns it turned). It was made using Node-RED. The turns count and angle value are published using Mqtt server in it.

Figure 34: Node-RED Dashboard

## Previously Used Code With Libraries

#include <avr/io.h>

#include <avr/interrupt.h>

#include <util/delay.h>

#include <Wire.h>

// Default I2C address of AS5600 Hall effect IC #define AS5600_ADDRESS 0x36
volatile char highByt;
volatile char lowByt;
float numberOfTurns = 0; // number of turns int fin;
int quadrantNumber = 0; // quadrant IDs
int previousQuadrantNumber = 0;
// commanda to say what to do with incoming data volatile byte command = 0;
void setup() {
// have to send on master in, *slave out* DDRB |= (1 << DDB4); // Set MISO as OUTPUT // turn on SPI in slave mode
SPCR |= (1 << SPE);
// turn on interrupts
SPCR |= (1 << SPIE);
Wire.begin();
}
void getTurns(){
/*
//Quadrants:
4 | 1
3 | 2
*/
// Quadrant 1 if (fin >= 0 && fin <= 90) { quadrantNumber = 1;
}
// Quadrant 2
if (fin > 90 && fin <= 180) { quadrantNumber = 2;
}
// Quadrant 3
if (fin > 180 && fin <= 270) { quadrantNumber = 3;
}
// Quadrant 4
if (fin > 270 && fin < 360) {
quadrantNumber = 4;
}
if (quadrantNumber != previousQuadrantNumber){ // if we changed quadrant if (quadrantNumber == 1 && previousQuadrantNumber == 4) { numberOfTurns++; // 4 --> 1 transition: CW rotation }
if (quadrantNumber == 4 && previousQuadrantNumber == 1) { numberOfTurns--; // 1 --> 4 transition: CCW rotation
}
previousQuadrantNumber = quadrantNumber; //update to the current quadrant
}
totalAngle = (numberOfTurns * 360) + fin; //number of turns (+/-) plus the actual angle within the 0-360 range
}
}
// SPI interrupt routine
ISR(SPI_STC_vect) {
byte c = SPDR;
switch (command) {
// no command? then this is the command case 0:
command = c;
SPDR = 0;
break;
// first byte
case | 1 | :
SPDR = highByt;
break;
// second byte
case | 2 | :
SPDR = lowByt;
break;
// third byte - turns count
case | 3 | :
SPDR = lowByt;
break;
} // end of switch

} // end of interrupt service routine (ISR) SPI_STC_vect void loop() {
// if SPI not active, clear current command if (PINB & (1 << PINB2)) { // Read SS pin
command = 0;
}
_delay_ms(100);
Wire.beginTransmission(AS5600_ADDRESS);
Wire.write(0x0D); // Send the address of the raw angle register Wire.endTransmission();
Wire.requestFrom(AS5600_ADDRESS, 1); // Request 1 byte of data _delay_ms(100);
while (Wire.available()) {
lowByt = Wire.read(); // Read the low byte
}
_delay_ms(100);
Wire.beginTransmission(AS5600_ADDRESS);
Wire.write(0x0C); // Send the address of the raw angle register Wire.endTransmission();
Wire.requestFrom(AS5600_ADDRESS, 1); // Request 1 byte of data _delay_ms(100);
while (Wire.available()) {
highByt = Wire.read(); // Read the high byte
}
_delay_ms(100);
}
int main() {
setup();
// Enable global interrupts sei();
while (1) {
loop();
}
return 0;
}

### This documentation has been reviewed by Group H - Obstacle Avoidance System

for Warehouse AMR and Obstacle Avoidance System for Warehouse AGV.

Name | Signature
1. Kuruppu M. P.
2. Peiris D. L. C. J.
3. Herath B. H. M. K. S. B.
4. Madushan I. D.

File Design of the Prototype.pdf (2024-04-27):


### Department of Electronic and Telecommunication Engineering University of Moratuwa

### Design of the Prototype

## Multi-turn Absolute Magnetic Encoder

Epa Y.L.A. | 210156U
Epa Y.R.A. | 210157A

This report is submitted as a partial fulfilment of module EN2160

April 2024

Design of Prototype

### Contents

1 User Requirements | 3
2 Conceptual Designs and Functional Block Diagrams | 4
3 Complete Comparison | 6
4 Evaluation Criteria | 6
5 Selected Design | 7
6 Final Solidworks Design | 7
7 Final Schematic Design | 8
8 Final PCB Design | 15

### 1 User Requirements

- Absolute Positioning
The encoder should be able to provide the absolute angular position of the shaft over multiple turns, accurately indicating its position.
- Multi-Turn Capability
The encoder should be capable of tracking multiple revolutions of the shaft, allowing users to determine the absolute position across several complete rotations.
- Accuracy
Accuracy of the encoder is essential where precise positioning is critical. Specific tolerance should be defined based on the requirements.
- Resolution
The encoder should offer resolution sufficient enough for the requirement of the user to detect even minor changes in position.
- Reliability
The device should provide the same accuracy of angle data over a long period of time and each and every time the output should be the same for a specific position.
- Operating Range
The encoder must operate effectively within a specified range of temperature and other environmental conditions. The operating range should be defined based on the expected conditions in the application environment.
- Communication Interface
The encoder should support commonly used communication protocols to transmit the encoder output data.
- Size
The encoder should fit within the physical constraints of the application. Also it should be relatively small for it to be accommodated by the motor.
- Fast Response Time
Users may require the encoder to provide position information quickly, especially in applications where rapid changes in position occur.
- Cost-effectiveness
One of the main concerns of the user is the cost per item. It should be as minimum as possible while also maintaining the functionality upto a certain standard.
- Power Requirements
The encoder should operate within a specified power supply range and should have low power consumption to ensure energy efficiency.
- Lifespan and Maintenance
Users typically require a long lifespan with minimal maintenance. It should be able to withstand the expected usage without requiring frequent repairs or replacements.

### 2 Conceptual Designs and Functional Block Diagrams


Figure 1: Conceptual Design 1


Figure 2: Functional Block Diagram for Conceptual Design 1


Figure 3: Conceptual Design 2


Figure 4: Functional Block Diagram for Conceptual Design 2

Figure 5: Conceptual Design 3

Figure 6: Functional Block Diagram for Conceptual Design 3

### 3 Complete Comparison

| Conceptual design 1 | Conceptual design 2 | Conceptual design 3
Newly added fea-tures | Multi turn capabil-ity using wiegand sensor which doesn’t require power to op-erate | Multi turn capabil-ity using Gear box and two hall effect sensor ICs | Multi turn counting using the microcon-troller and one hall effect sensor
Removed features | Removed the neces-sity to give inter-nal power for the circuitry to function during power out-ages | removed the need for wiegand sensor | removed extra sen-sors and circuitry to address the multi turn capability
Enclosure design cri-teria comparison: 1. Functionality 2. Size and weight 3. Ergonomic 4. Heat dissipation 5. Mounting and alignment 6. Simplicity | 9 9 8 8 8 7 | 9 5 7 6 6 6 | 9 8 8 8 8 8
Functional block de-sign criteria compar-ison: 1. Functionality 2. Requirements 3. Power consump-tion 4. Future proofing 5. Cost 6. Manufacturing feasibility | 8 7 9 6 6 5 | 9 9 8 6 4 4 | 8 7 8 8 9 8
Total | 90 | 79 | 97

### 4 Evaluation Criteria

Enclosure Design Criteria:

1. Functionality: How well does the design support internal functionality?
2. Size and weight: How compact and lightweight is the enclosure for easy integration?
3. Ergonomics: How well does the enclosure design allow for easy handling installation and maintenance?
4. Heat dissipation: How much heat is generated and how well it has been managed?
5. Mounting and alignment: How easy is it to mount and align the encoder with the shaft, and how well does the enclosure maintain its alignment?
6. Simplicity

Functional Block Diagram Criteria:

1. Functionality: How well the circuit design meets functional requirements such as resolution, accuracy, and speed?
2. Requirements: How well does the components (magnet, hall effect sensors, etc) meet the requirements for accuracy and resolution?
3. Power consumption: How efficiently does the design manage power consumption?
4. Future proofing: To what extent does the design allow for easy replacement or upgrade of individual components?
5. Cost: Overall cost effectiveness for the provided functionality
6. Manufacturing feasibility: Feasibility of manufacturing the design

### 5 Selected Design

From the above three designs, we have selected the final design. There are several reasons for this.

Design 1 included a wiegand sensor which isn’t available to purchase at small quantities. Even though we tried to find out an alternative part for that, we got no success.

Design 2 utilizes a gear box which isn’t practical because of the size. Also it will make the encoder complex and ultimately limit the number of multi turns which the encoder can count. Durability and the weight of the encoder is also affected because of this.

The third design is the option we can go for in this situation. A battery backup is used in this design to power the encoder every time and it’s charged when the main supply is available.

### 6 Final Solidworks Design

Solidworks design contains four main parts.


(a) Base | (b) Middle


(a) Housing | (b) Battery Holder


(c) Assembly

### 7 Final Schematic Design

There are 6 schematics sheets in our circuit. They are,
- Encoder Circuit (top sheet)
- Microcontroller Circuit
- Hall Effect IC Circuit
- Voltage Regulator Circuit
- Battery Protection Circuit
- Battery Charging Circuit

Title; MOSI; MISO; SCK; SCL; SDA; Microcontroller Circuit; +3V7 Battery; GND; VCC; Encoder Circuit; OUTPUT; PIJ101; PIJ102; PIJ103; PIJ104; PIJ105; PIJ106; COJ1

Number Revision Size

Date: 4/02/2024 Sheet of

File: F:\Altium Projects\..\Encode Schematic.SchDoc Drawn By:

Hall Effect IC Circuit

Voltage Regulator Circuit

Battery Protection Circuit

Battery Charging Circuit


File: F:\Altium Projects\..\Microcontroller.SchDoc Drawn By:

Title; VDD5V 1; VDD3V3 2 OUT 3; GND 4; DIR 8; SCL 7; SDA 6; PGO 5; AS5600-ASOM; GND; SCL; SDA

Number Revision Size

Date: 4/02/2024 Sheet of

File: F:\Altium Projects\..\Hall Effect IC.SchDocDrawn By:

Hall Effect IC

Title; VoltageRegulator; BYP 4; IN 1 OUT 5; GND 2; MIC5205-3.3YM5-TR; GND GND; GND; +3V7 Battery +3V7 Battery; Blue

Number Revision Size

Date: 4/02/2024 Sheet of

File: F:\Altium Projects\..\Voltage Regulator.SchDoc Drawn By:

Title; BATTERY IN; -3V7 Battery; GND; GND 6; VCC 5; +3V7 Battery; Battery ProtectionCircuit

Number Revision Size

Date: 4/02/2024 Sheet of

File: F:\Altium Projects\..\Battery Protection.SchDoc Drawn By:


File: F:\Altium Projects\..\Battery Charger.SchDoc Drawn By:


### 8 Final PCB Design

Our final PCB Design is of round shape and is only 36mm in diameter. We have used smd components to minimize the size of it.

(d) PCB Layout | (e) PCB Layout
(f) Top view | (g) Bottom view
(h) Side view | (i) Side view

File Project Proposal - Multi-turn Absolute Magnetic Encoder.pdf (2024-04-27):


Department of Electronic and Telecommunication Engineering University of Moratuwa

Project Proposal

## Multi-turn Absolute Magnetic Encoder

Epa Y.L.A. | 210156U
Epa Y.R.A. | 210157A

This report is submitted as a partial fulfilment of module EN2160

Feb 2024

### 1 Introduction

The aim of this project is to design and develop a multi-turn absolute magnetic encoder system. The encoder will provide accurate position feedback over multiple revolutions, making it suitable for applications requiring precise rotational positioning such as robotics, motor control, and industrial automation.

### 2 Methodology


Figure 1: Basic diagram: Reference [2]
Our methodology involves the following approach.
- Fixing a diametrically magnetized magnet onto the shaft (through the enclosure), enabling rotation
- Measuring the angle using the hall effect sensor, by considering the change in the magnetic polarity
- Tracking the number of revolutions completed by the magnet using the measured angle or a wiegand sensor

In order to achieve our goals, we plan on:

a) Selecting appropriate hardware including hall effect sensor ICs, microcontroller and diametrically magnetized magnets considering the cost and accuracy
b) Developing algorithms for absolute position calculation and multi-turn tracking
c) Testing the hardware and software to evaluate it’s accuracy, precision and reliability

### 3 Conclusion

Developing a multi-turn absolute magnetic encoder will provide a valuable solution for applications requiring precise rotational position sensing and control.

### 4 Reference

[1] “Magnetic Rotary Encoder Technology” [Online]. https://files.pepperl-fuchs.com/webcat/navi/productInfo/doct/tdoct3063 eng.pdf? v=20231211180839 (https://files.pepperl-fuchs.com/webcat/navi/productInfo/doct/tdoct3063__eng.pdf?v=20231211180839)
[2] “New Magnetic Rotary Encoder Technology” https://youtu.be/soImUGrWuhI
[3] “AS20-Series Miniature Encoder : Magnetic Absolute Kit Encoder with Energy Harvesting Multi-Turn.” [Online]. https://docs.broadcom.com/doc/AS20-M42M-Series-DS

2

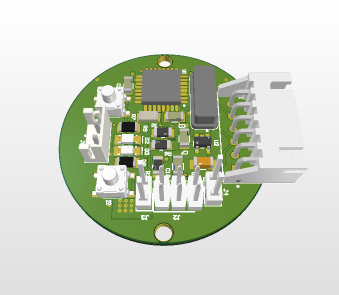
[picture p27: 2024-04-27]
PCB/Encoder PCB/Project Outputs for EDR/PCB_Photos/side1.png

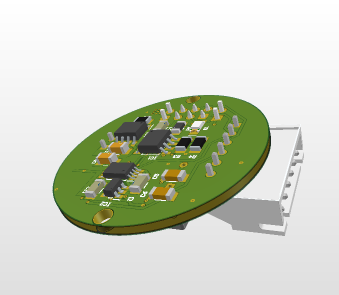
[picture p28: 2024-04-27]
PCB/Encoder PCB/Project Outputs for EDR/PCB_Photos/side2.png

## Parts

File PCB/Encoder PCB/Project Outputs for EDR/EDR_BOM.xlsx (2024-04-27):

Line # | Name | Description | Designator | Revision ID | Revision State | Revision Status | Quantity | Manufacturer 1 | Manufacturer Part Number 1 | Manufacturer Lifecycle 1 | Supplier 1 | Supplier Part Number 1 | Supplier Unit Price 1 | Supplier Subtotal 1
 | C1206C104J4GACAUTO | Capacitor | C1, C2, C3, C4, C7, C11 |  | Not managed |  | 6
 | GRM0335C1E220JA01D | Chip Multilayer Ceramic Capacitors for General Purpose, 0201, 22pF, C0G, 30ppm/°C, 5%, 25V | C5, C6 | CMP-2010-01342-3 | New From Design | Up to date | 2 | Murata | GRM0335C1E220JA01D | Volume Production | Mouser | 81-GRM0335C1E220JA1D | 0.006 | 0.06
 | GMK316AB7106KL-TR | None | C8, C9 | CMP-2000-06324-3 | Released | Up to date | 2 | Taiyo Yuden | GMK316AB7106KL-TR | Not Recommended for New Design | Future Electronics | 3103948 | 0.435 | 0.87
 | C1206C104K1RACTU | CAP CER 0.1UF 100V X7R 1206 | C10 | CMP-03020-000153-1 | New From Design | Up to date | 1 | KEMET | C1206C104K1RACTU | Volume Production | Mouser | 80-C1206C104K1R | 0.15 | 0.15
 | GRM31CR61H106KA12L | CAP CER 10UF 50V X5R 1206 | C12 | CMP-2000-05256-2 | New From Design | Up to date | 1 | Murata | GRM31CR61H106KA12L | Obsolete | Arrow Electronics | GRM31CR61H106KA12L | 0.3724 | 744.8
 | 150120VS75000 |  | D1 | CMP-1426-00016-2 | Released | Up to date | 1 | Wurth Electronics | 150120VS75000 | Volume Production | Digikey | 732-4993-1-ND | 0.23 | 0.23
 | APT3216CGCK | LED | D2 |  | Not managed |  | 1
 | 150120AS75000 |  | D3 | CMP-1426-00018-2 | Released | Up to date | 1 | Wurth Electronics | 150120AS75000 | Volume Production | Digikey | 732-4988-1-ND | 0.23 | 0.23
 | AS5600-ASOM | Integrated Circuit | IC1 |  | Not managed |  | 1
 | DW01A-G | Integrated Circuit | IC2 |  | Not managed |  | 1
 | S6B-XH-A (LF)(SN) | CONN HEADER R/A 6POS 2.5MM | J1 | CMP-17439-000165-2 | New From Design | Up to date | 1 | JST | S6B-XH-A(LF)(SN) | Volume Production | Future Electronics | 7178361 | 0.182 | 0.182
 | 90131-0763 | Connector | J2 |  | Not managed |  | 1
 | 87527-2 | Power isolation jumper | J3, J4 |  | Not managed |  | 2
 | B2B-EH-A(LF)(SN) | CONN HEADER VERT 2POS 2.5MM | J5 | CMP-17439-000026-1 | New From Design | Up to date | 1 | JST | B2B-EH-A(LF)(SN) | Volume Production | Future Electronics | 9177935 | 0.0528 | 0.0528
 | TP4056 | Connector | J6 |  | Not managed |  | 1
 | FS8205A | MOSFET (N-Channel) | Q1 |  | Not managed |  | 1
 | RP73D2B10KBTG | Res Thin Film 1206 10KΩ 0.1% 0.25W 15ppm/°C Molded SMD | R1, R2, R5 | CMP-03211-008372-1 | New From Design | Up to date | 3 | TE Connectivity Holsworthy | RP73D2B10KBTG | Volume Production | Newark | 51R8326 | 0.17 | 0.51
 | CRGH2512J4K7 | Resistor | R3, R4 |  | Not managed |  | 2
 | RNCP1206FTD100R | 100Ω ±1% 0.5W 1206 High Power Anti-Sulfur Thin Film Chip Resistor | R6 | CMP-26527-003782-1 | New From Design | Up to date | 1 | Stackpole Electronics | RNCP1206FTD100R | Volume Production | Arrow Electronics | RNCP1206FTD100R | 0.0884 | 0.0884
 | RCS12061K00JNEA | Resistor | R7 |  | Not managed |  | 1
 | CRCW1206680RFKEA |  | R8, R9 | CMP-2003-02340-1 | Released | Up to date | 2 | Vishay | CRCW1206680RFKEA | Volume Production | Newark | 42K5172 | 0.011 | 0.022
 | RC1206FR-071K2L | Resistor | R10 |  | Not managed |  | 1
 | 1-1825910-0 | SWITCH TACTILE SPST-NO 0.05A 24V | SW1, SW2 | CMP-03407-000018-1 | New From Design | Up to date | 2 | TE Connectivity | 1-1825910-0 | Volume Production | Mouser | 506-FSM6JH | 0.14 | 0.28
 | ATmega88PA-AU | 8-bit AVR Microcontroller, 8KB Flash, 512 Bytes EEPROM, 1KB SRAM, 32-pin TQFP, Industrial Grade (-40°C to 85°C) | U1 | CMP-0095-00213-2 | Released | Up to date | 1 | Microchip | ATMEGA88PA-AU | Unknown | Arrow Electronics | ATMEGA88PA-AU | 1.79 | 1.79
 | MIC5205-3.3YM5-TR | IC REG LINEAR 3.3V 150MA SOT23-5 | U2 | CMP-06324-000014-1 | New From Design | Up to date | 1 | Microchip | MIC5205-3.3YM5-TR | Volume Production | Newark | 52AH1168 | 0.382 | 0.382
 | 6I08000F20UCG | Crystal or Oscillator | Y1 |  | Not managed |  | 1

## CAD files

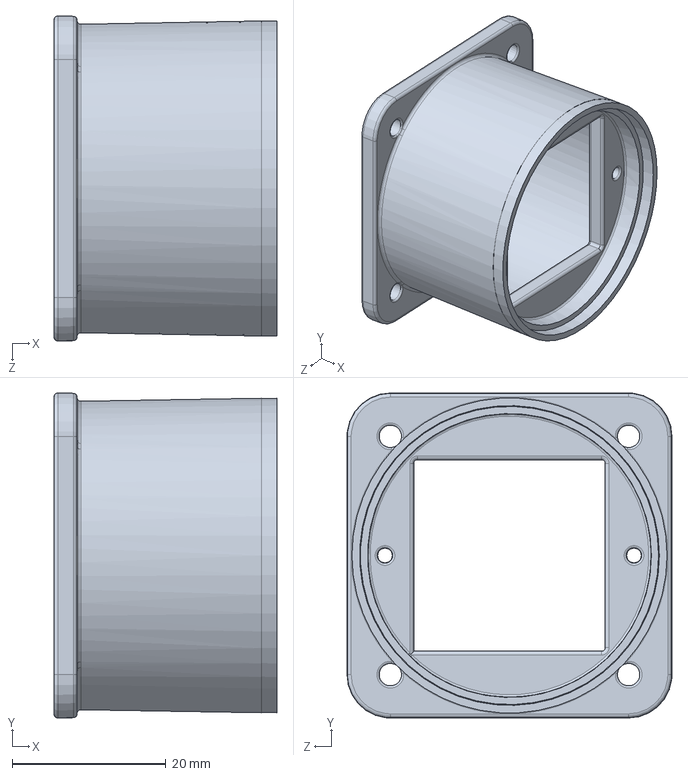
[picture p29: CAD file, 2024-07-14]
Enclosure/Main Base.SLDPRT
29.0 x 42.3 x 42.3 mm

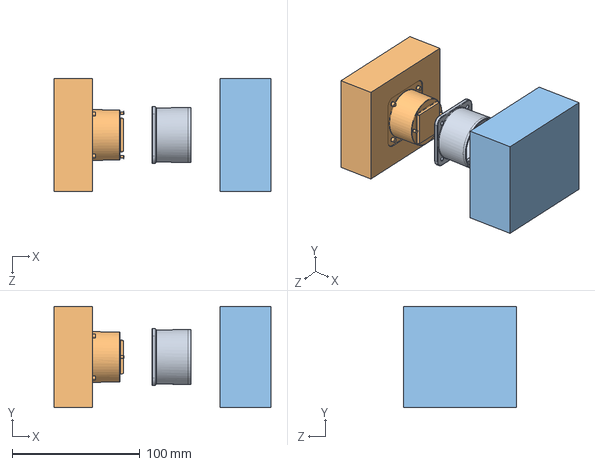
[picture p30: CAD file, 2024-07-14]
Molds/base/shitasm.SLDASM
169.6 x 79.0 x 88.5 mm

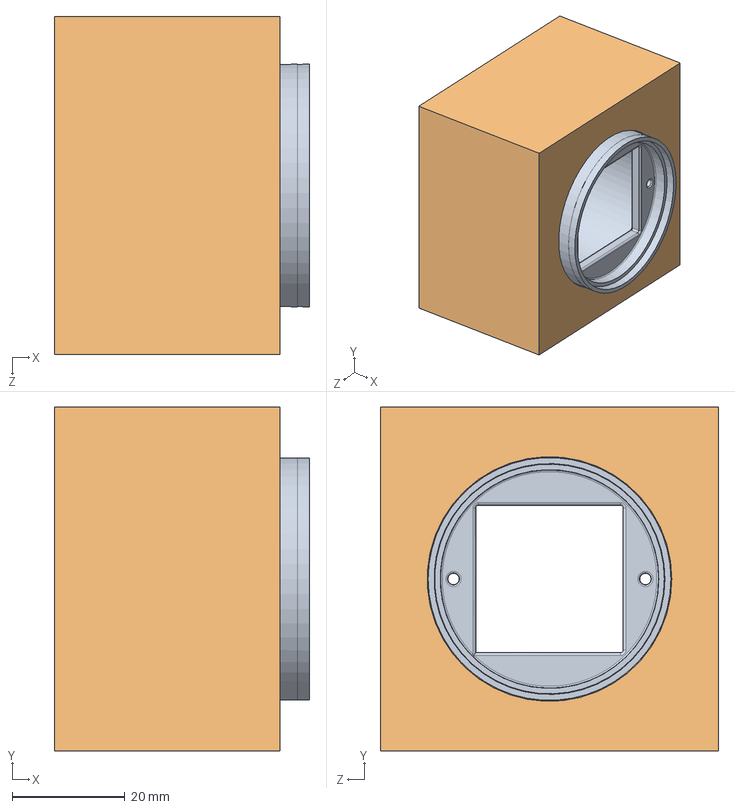
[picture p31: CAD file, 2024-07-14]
Molds/base/Assem2.SLDASM
45.2 x 61.0 x 60.0 mm

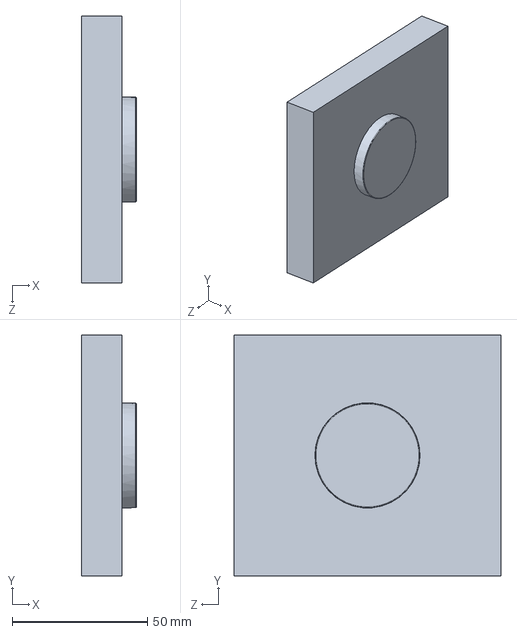
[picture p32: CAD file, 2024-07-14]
Molds/lid/Tooling Split1_15mm[1].SLDPRT
20.2 x 89.1 x 98.8 mm

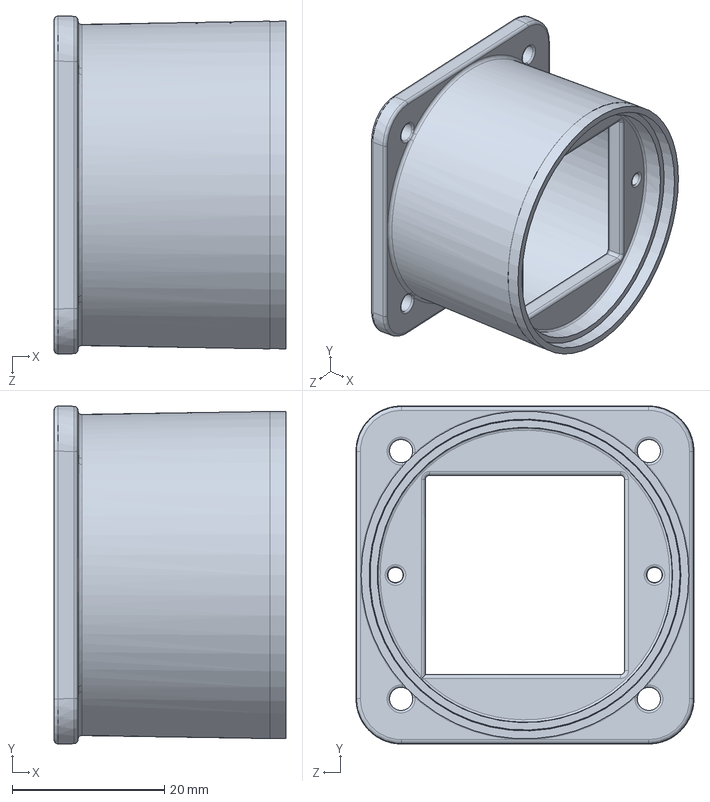
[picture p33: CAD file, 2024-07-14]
Molds/necutmodifiedbase.SLDPRT
30.5 x 44.4 x 44.4 mm

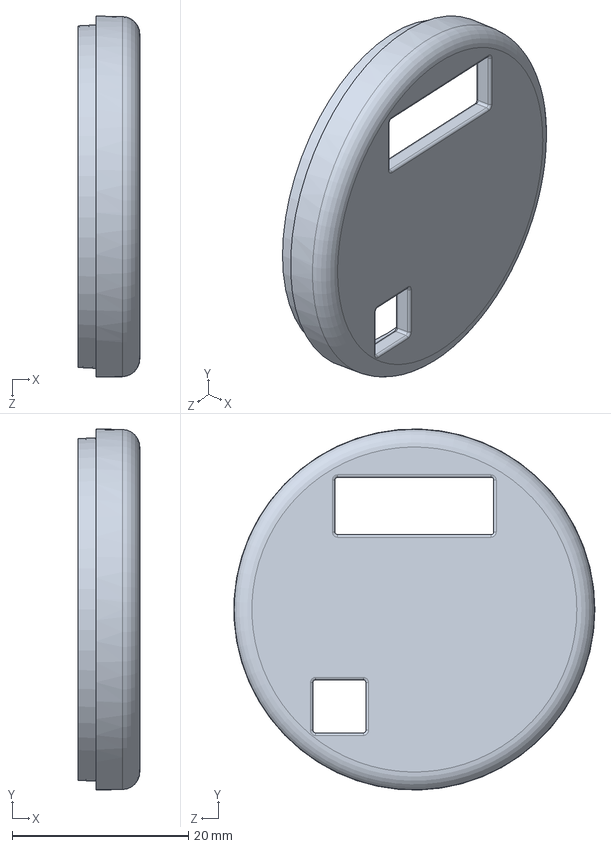
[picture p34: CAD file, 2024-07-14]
Enclosure/Lid.SLDPRT
7.00 x 41.0 x 41.0 mm

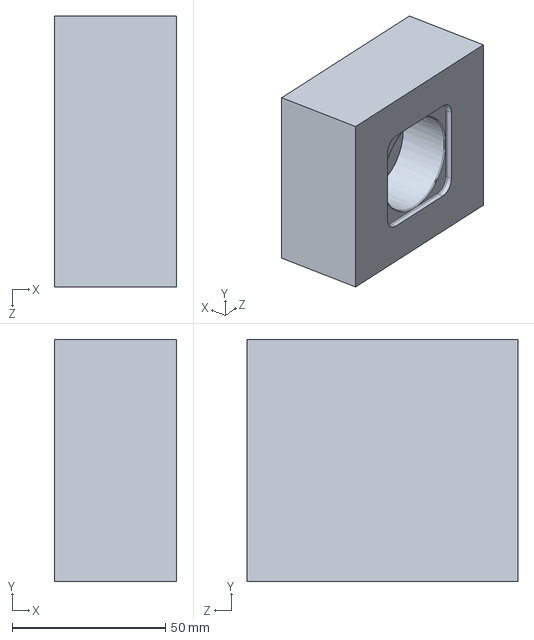
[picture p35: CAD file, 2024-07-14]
Molds/base/Tooling Split1[2].SLDPRT
40.0 x 79.0 x 88.5 mm

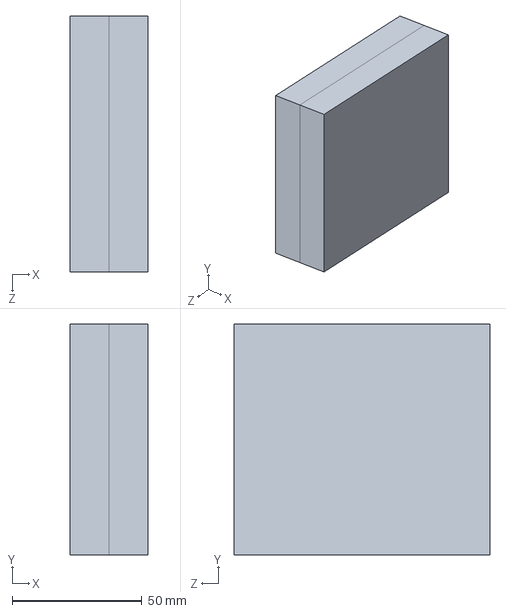
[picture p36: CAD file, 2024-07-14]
Molds/lid/modified cut draft angle.SLDPRT
30.0 x 89.1 x 98.8 mm

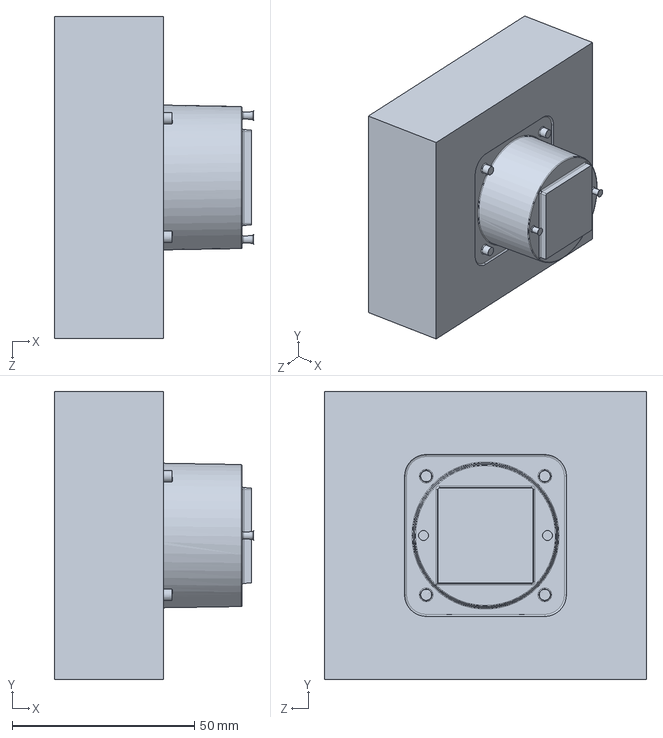
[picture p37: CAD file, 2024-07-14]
Molds/base/shit.SLDPRT
54.7 x 79.0 x 88.5 mm

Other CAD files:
Molds/lid/Tooling Split1_15mm[2].SLDPRT
Molds/lid/Parting Line1_.SLDPRT
Molds/base/Tooling Split1[1].SLDPRT
Molds/base/Scale1_1.05.SLDPRT

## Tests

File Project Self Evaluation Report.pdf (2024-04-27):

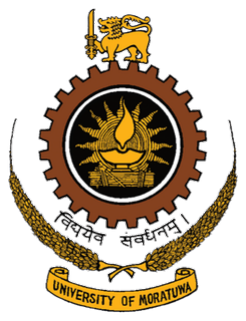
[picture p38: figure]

Department of Electronic and Telecommunication Engineering University of Moratuwa

Project Self Evaluation Report

### Multi-turn Absolute Magnetic Encoder

Epa Y.L.A. | 210156U
Epa Y.R.A. | 210157A

This report is submitted as a partial fulfilment of module EN2160

Feb 2024

We are making a multi-turn absolute magnetic encoder for this project. These encoders can count the angle revolved along with the number of total revolutions up to that point. They are mostly used in industrial machines where precise motion control is required along with the exact rotations did. Specially after a power failure, the knowledge of the exact position of the motor’s shaft is crucial to ensure the safety in some applications.

(1) Apply what you learn as engineering principles during last three semesters.

We should consider the user’s needs in making this encoder. It should be reliable and should provide the correct angle output in top of all. It’s also desirable to get some feedback after making this encoder and testing it. Also, we need to consider the efficiency and feasibility of the circuit. It is also desirable to make our encoder with proper quality and performance to be presented as a fine engineering product.

(2) Apply Mathematics and Science you learned during your A/L and last three semesters.

For this project we have many Mathematics and Science knowledge in practice. As the main objective of the encoder, we have to know the correct angular position of the shaft. Also we can calculate the angular velocity and we need calculus for this. Since this is a magnetic encoder, we can use linear algebra to analyse the magnetic field of the encoder using vectors and it’s effect. We also have to use the knowledge of torque and friction to study the motion of the shaft.

Moreover, we have to apply the theories of electromagnetics to understand the magnetic field of the encoder and more things about it like flux. More importantly, we have to use all the knowledge about electronics we learnt throughout our first three semesters to do this project.

(3) Apply hands on skills you learn during last three semesters.

We apply the hands on skills we learnt during the last three semesters in many aspects. Programming, soldering and circuit designing, simulation, testing, designing PCBs and enclosures are the major skills we use here. Circuit design skills are used when implementing a circuit that can power the encoder, read sensor signals and communicate with the controller. Programming is used when writing the code for controller. Other skills come to use when testing and implementing the circuit.

(4) Applicability of your project for solving an industrial problem in Sri

Lanka.

Our project can reduce the dependency on imported encoders and save foreign exchange while having all the benefits of a multi turn absolute magnetic encoder. By improving the accuracy and precision of the encoder in measuring the rotational position and speed of equipments such as robots and conveyors, and we can enhance the efficiency and performance of the industrial processes.

(5) The cost of main items needed are within the budget (what you can spend as a team)

We have identified main components needed for this project. One of the main ones is the hall effect sensor. Also, magnets, encoder disc, microcontrollers, PCB and a proper enclosure will be the main costs in this project. All of these fall within the budget constraints of our team.

(6) Suitability of the project to achieve the learning outcomes of the EDR course.

This project involves creating schematic diagrams, layout designs and circuit simulations, and then following the best practices and guidelines for PCB design with industry standards. It also involves considering the factors such as size, shape and material that affect the appearance, functionality, and usability of the encoder.

We need to prepare documents on design specifications, schematics, layout files and user manuals that describe the design process, components, features, and operation of the encoder. This is a real-world scenario where we have to design, test, and document an encoder that meets the customer’s needs and expectations, and then demonstrate its functionality and performance. So most of the learning outcomes of EDR course are achieved by this project.

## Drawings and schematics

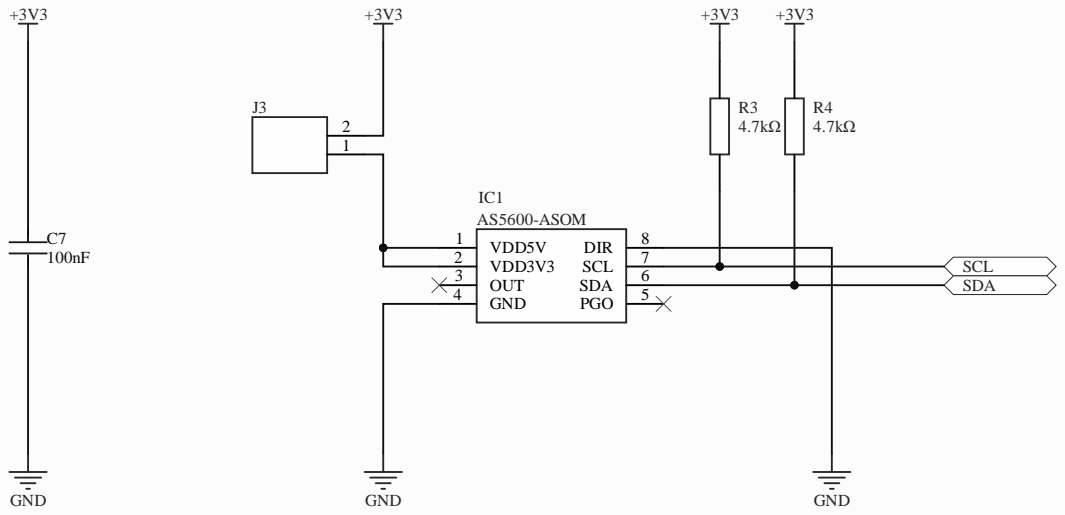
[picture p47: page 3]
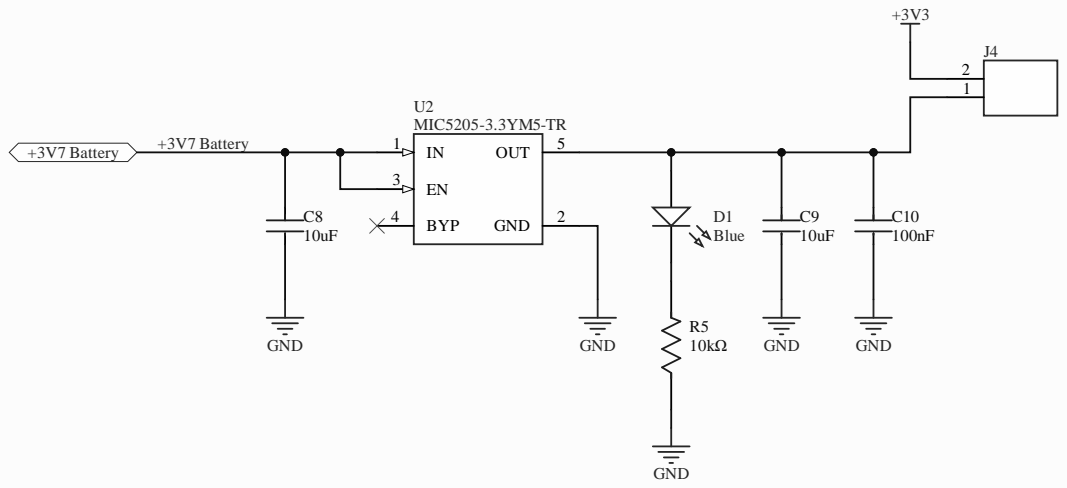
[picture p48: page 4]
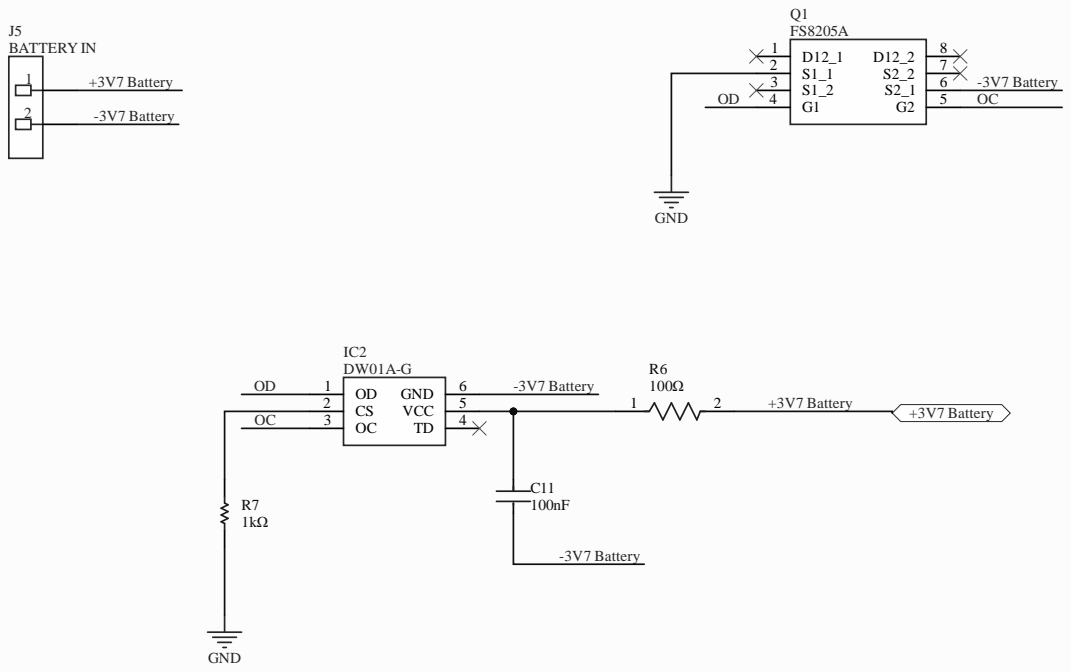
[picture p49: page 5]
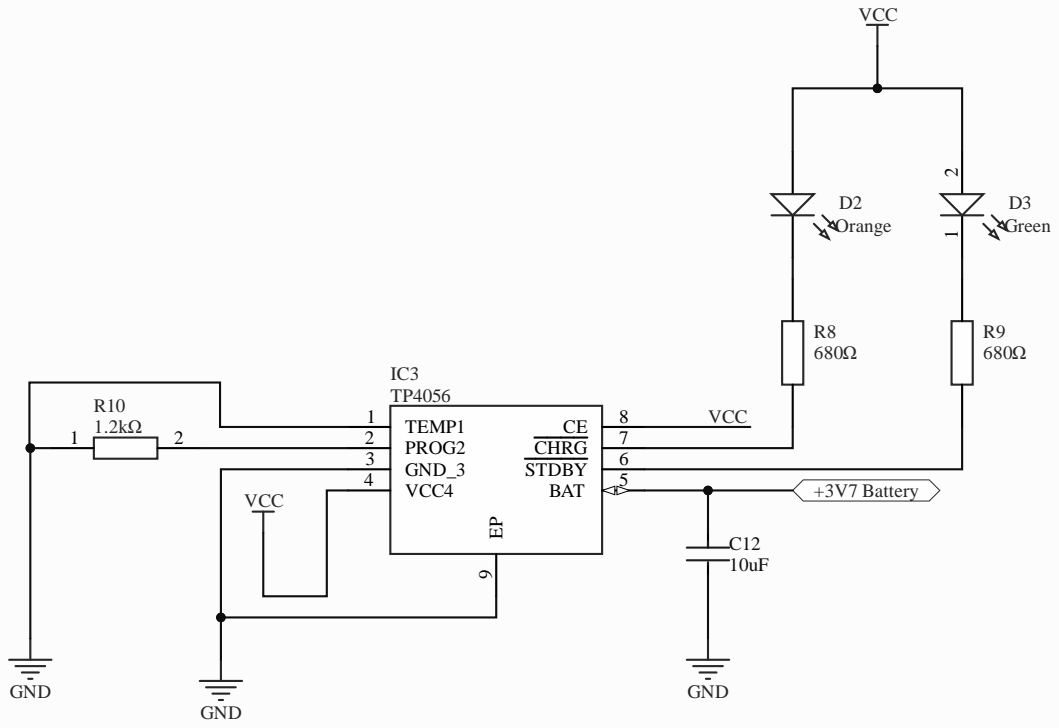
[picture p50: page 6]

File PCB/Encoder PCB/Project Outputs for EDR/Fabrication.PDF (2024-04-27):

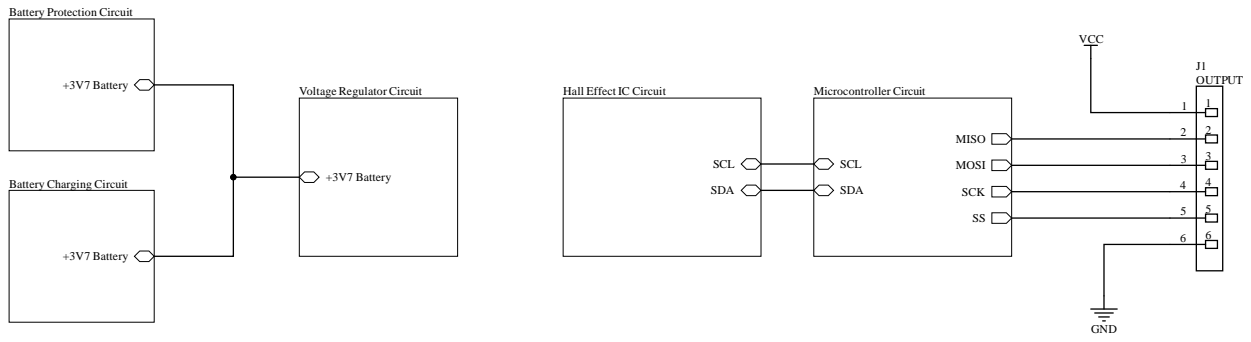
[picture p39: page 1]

Hall Effect IC Circuit

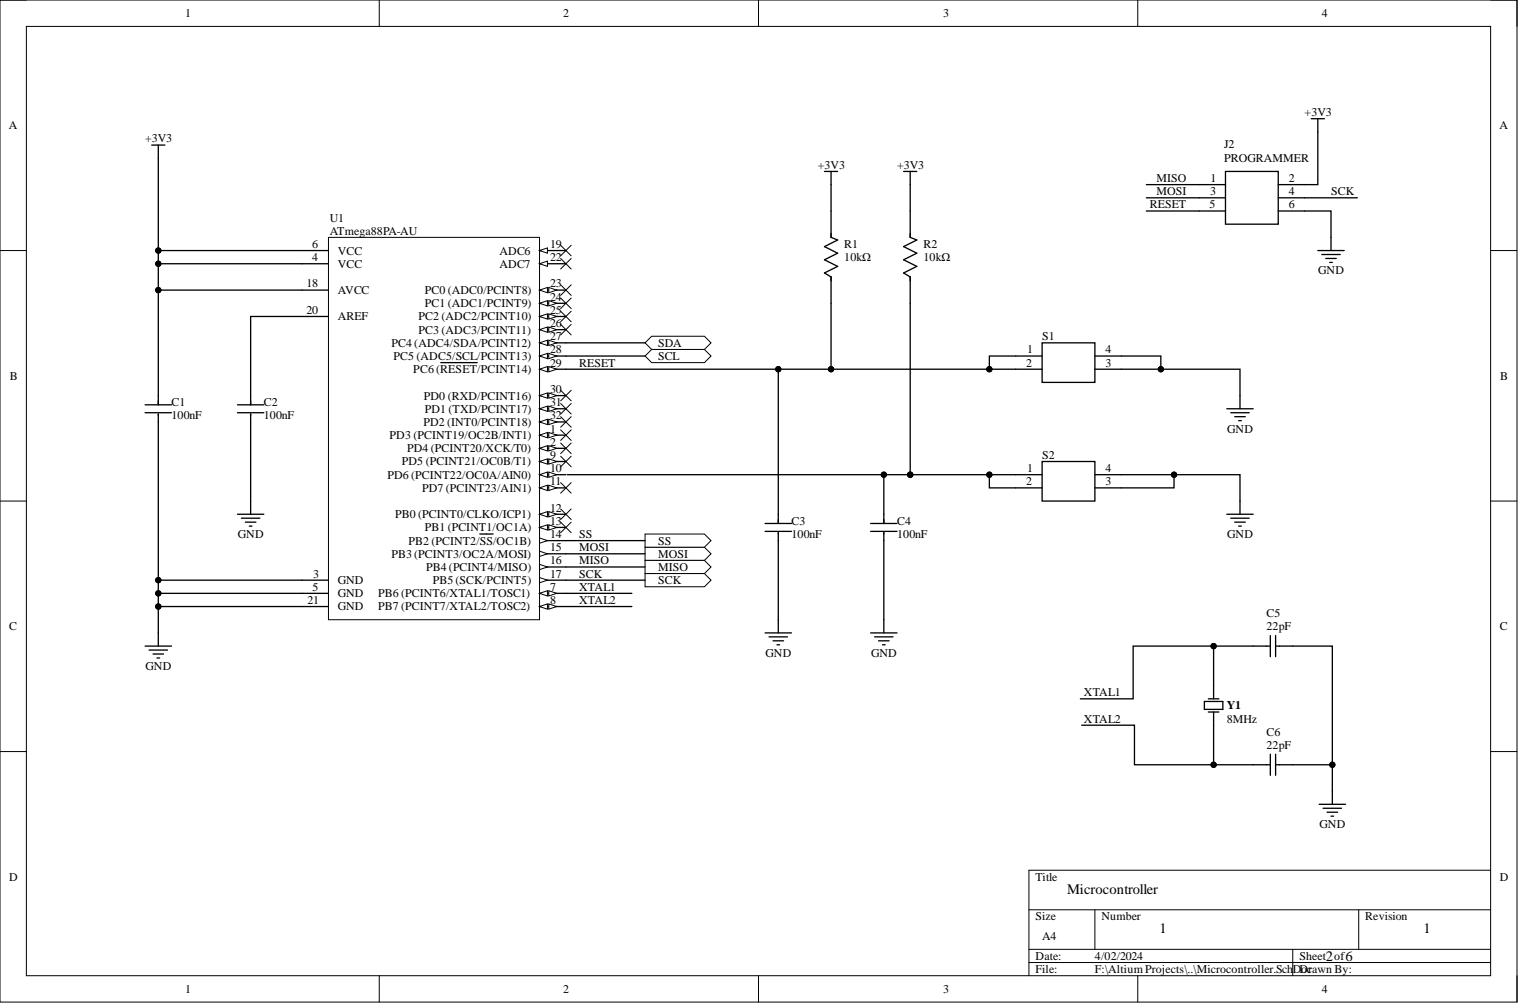
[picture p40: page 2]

1 8
2 0 | 2 4

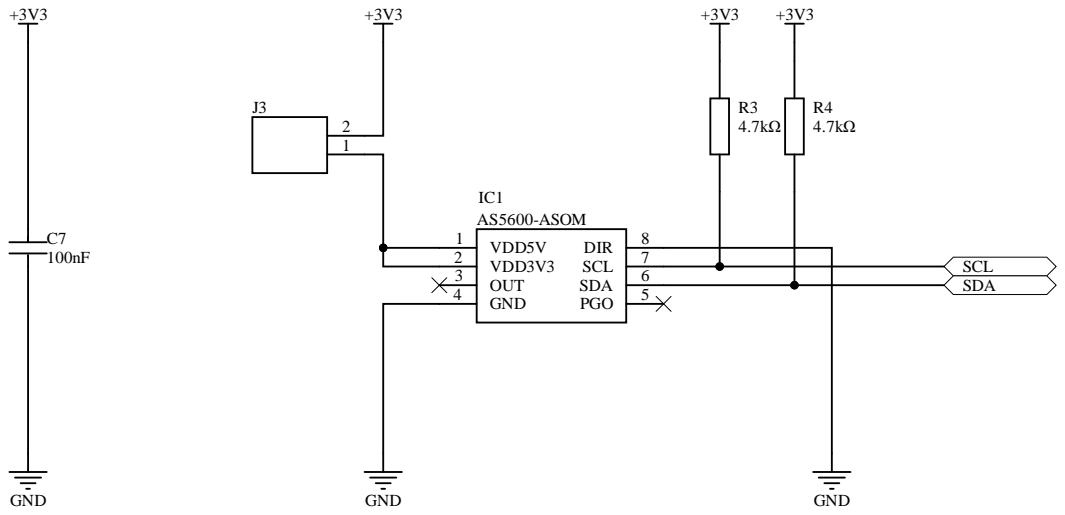
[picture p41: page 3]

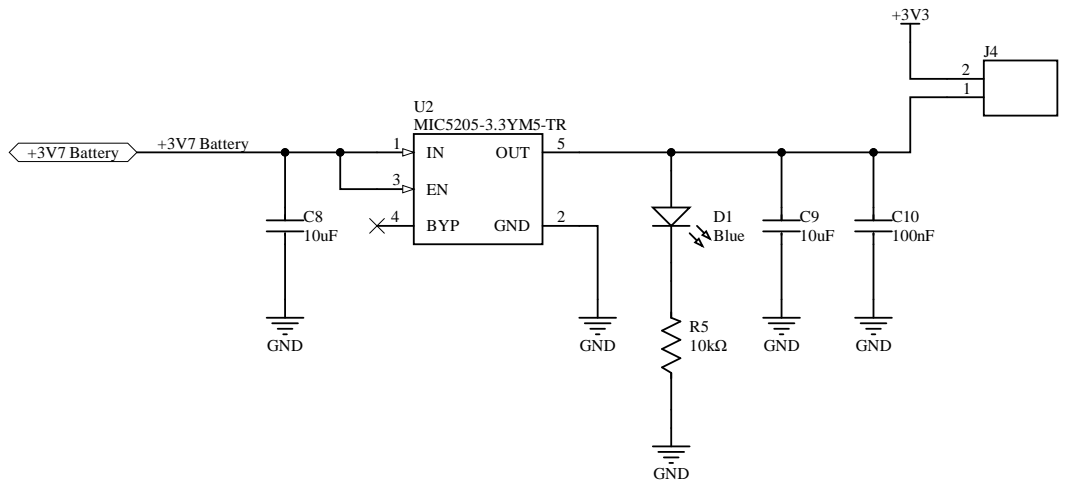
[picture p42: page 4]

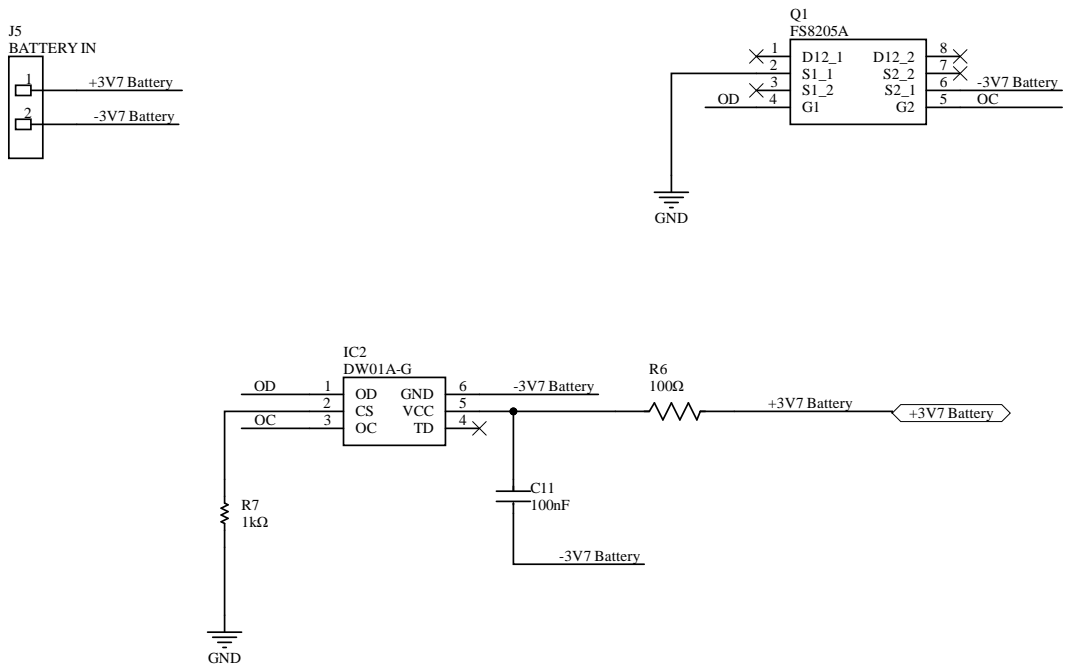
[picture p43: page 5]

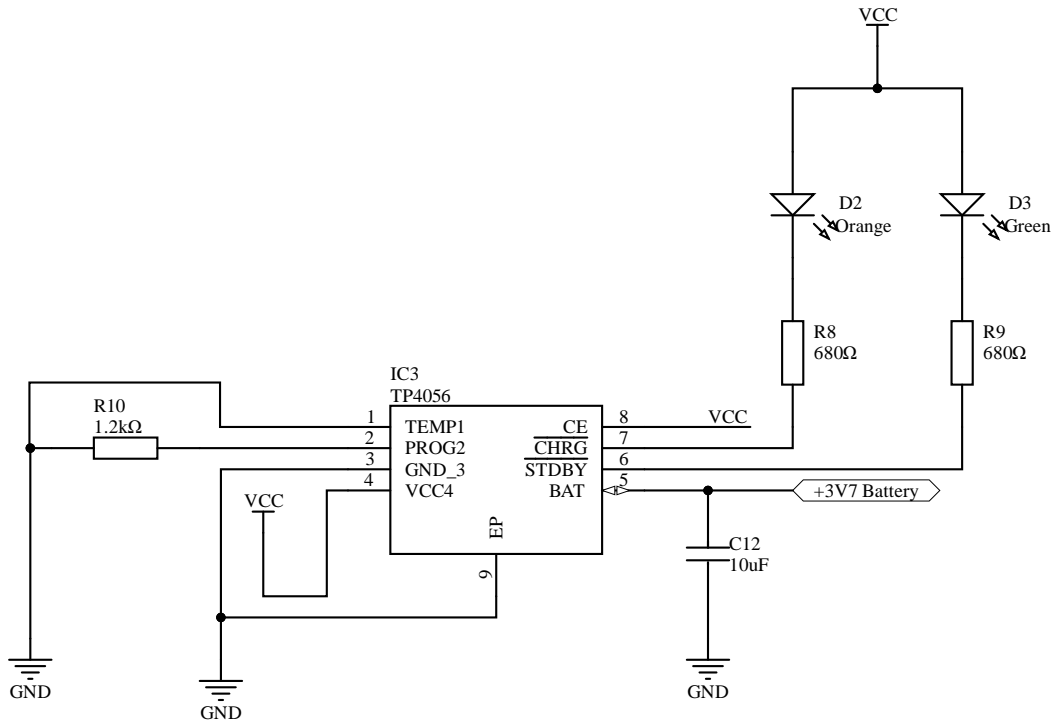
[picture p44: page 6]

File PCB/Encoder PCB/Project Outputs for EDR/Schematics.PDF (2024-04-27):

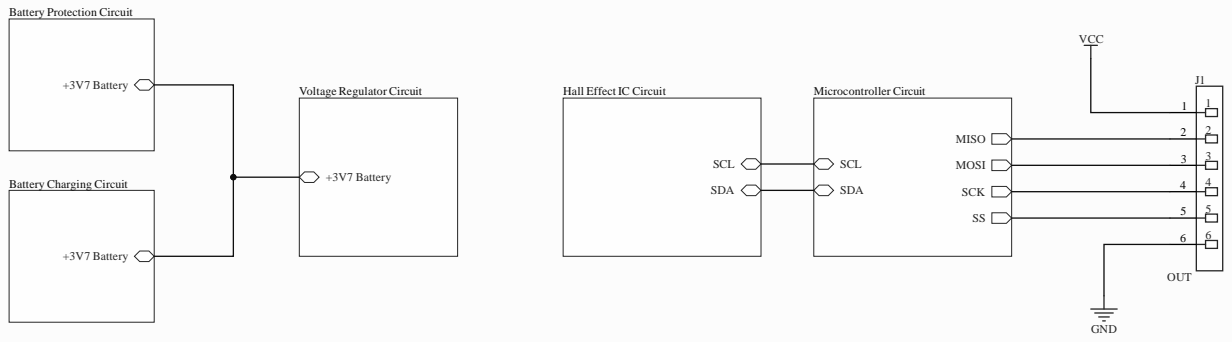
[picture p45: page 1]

Hall Effect IC Circuit

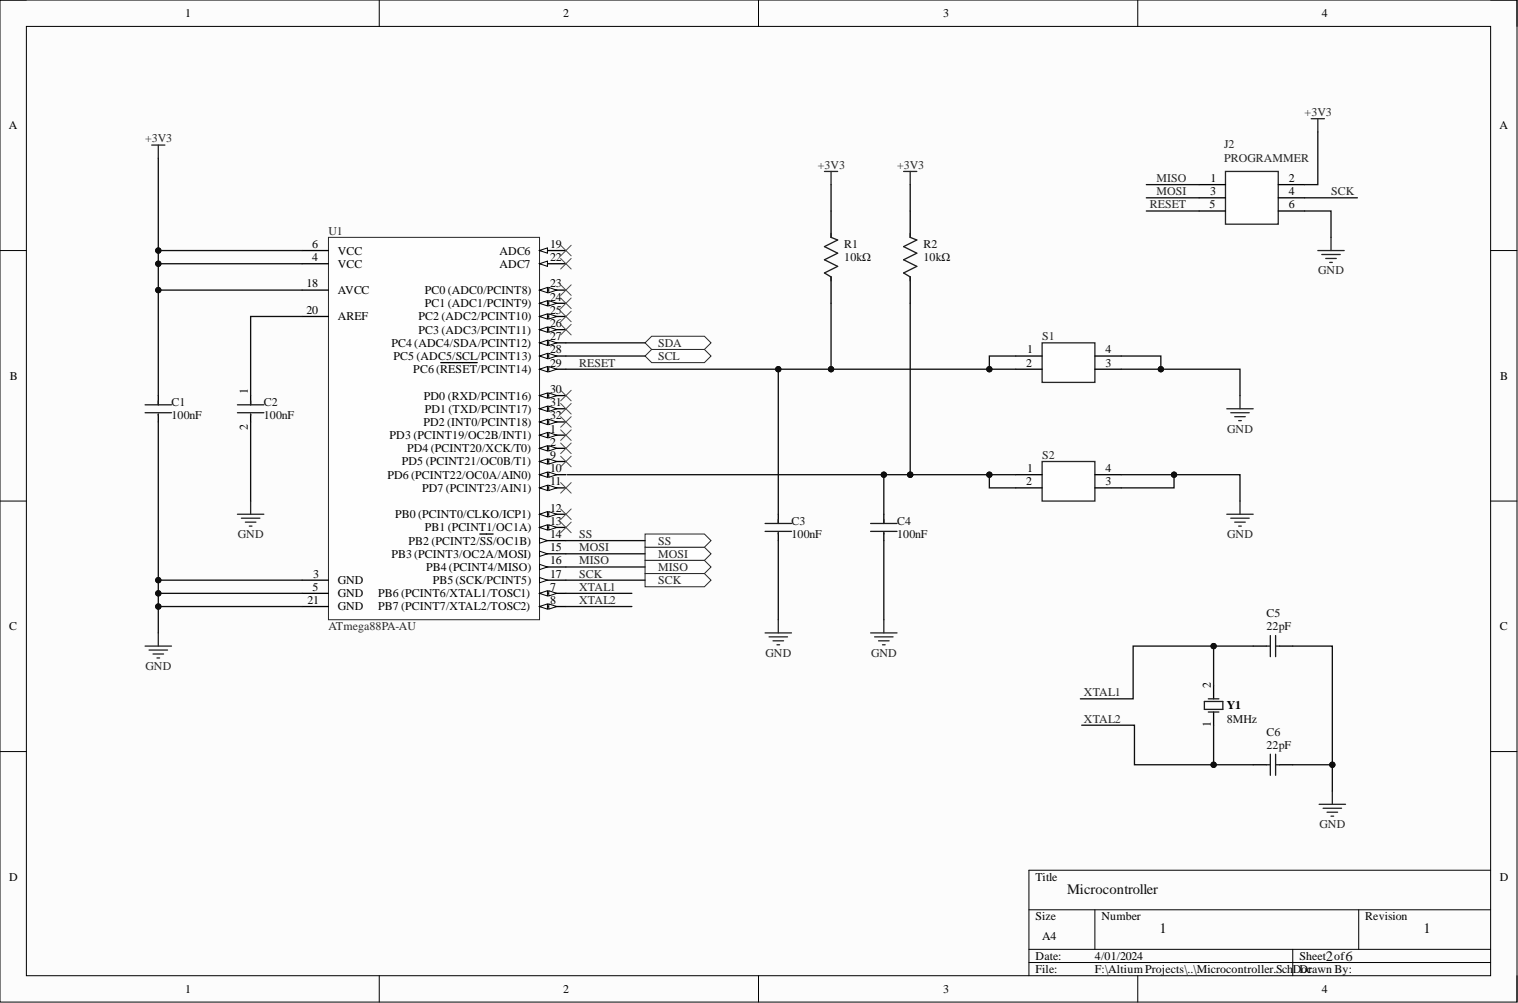
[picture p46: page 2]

1 8
2 0 | 2 4
